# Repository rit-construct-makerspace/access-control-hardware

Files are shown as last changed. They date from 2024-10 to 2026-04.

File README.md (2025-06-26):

# Makerspace Access Control System

## Summary
There's a lot of equipment in a makerspace that can be dangerous to operate without proper training. To make sure only trained personnel are accessing equipment at the RIT SHED Makerspace, an access control system was developed. This system works off of student/faculty/staff NFC ID cards, and checks a central database (automatically updated by training programs) to ensure users are trained to use the machine they are trying to access. A number of different switching mechanisms are developed, to allow maximum flexibility in integration with a wide array of machines. 

### More information can be found on the [GitHub Wiki](https://github.com/rit-construct-makerspace/access-control-hardware/wiki).

### Firmware documented in a seperate repository; [access-control-firmware](https://github.com/rit-construct-makerspace/access-control-firmware).

## Current State
All components of the Access Control System have reached a stable and mature release, and are ready undergoing large-scale deployment testing across all 3 of our makerspaces.

## Instructions & Further Documentation
[See the wiki on GitHub!](https://github.com/rit-construct-makerspace/access-control-hardware/wiki) 

## Photos & Media
Coming Soon!

## License
This project is licensed under the CERN-OHL-S License. See LIECENSE.txt for more information.

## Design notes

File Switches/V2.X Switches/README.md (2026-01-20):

# V2.X Switch Backwards Compatibility

ACS version 2.X Switches are backwards compatible with ACS version 3.X Cores and similar. A DB9 to HD15 adapter for converting PS2 video to VGA video can be used to adapt the interface. The following pins of the DB9 are connected in these adapters;

* DB9 (Pin) - HD15 (Pin)
* 1 (Access) - 1 (Access)
* 2 (OneWire) - 2 (OneWire)
* 3 (Ground) - 3 (Ground)
* 4 (Power) - 13 (+5V)
* 5 (Ground) - Not Connected
* 6 (Type) - 6 (+5V)
* 7 (Interrupt) - 7 (Interrupt)
* 8 (Unused) - Not Connected
* 9 (Unused) - 10, 11 (Ground)

This is only suggested with short cable runs, as there is already a >500mV voltage drop from the switch's diode.

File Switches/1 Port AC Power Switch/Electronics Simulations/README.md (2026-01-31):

These files are meant to be opened in Falstad Circuit Simulator. See https://www.falstad.com/circuit/ for more information.

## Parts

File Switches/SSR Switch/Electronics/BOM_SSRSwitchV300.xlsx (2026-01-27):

No. | Quantity | Comment | Designator | Footprint | Value | Manufacturer Part | Manufacturer | Supplier Part | Supplier
1 | 2 | 100nF | C1,C2 | C0805 | 100nF | CL21B104KCFNNNE | SAMSUNG(三星) | C28233 | LCSC
2 | 1 | DS1038-15FBNSiA74-0CC | CN1 | DSUB-TH_DS1038-15FBNSIA74-0CC |  | DS1038-15FBNSiA74-0CC | CONNFLY | C75754 | LCSC
3 | 1 | XY308-2.54-5P | CN2 | CONN-TH_XY308-2.54-5P |  | XY308-2.54-5P | XINLAIYA(新莱亚) | C915914 | LCSC
4 | 1 | 921-111A1010D10200 | CN3 | USB-B_TH_USB-B-FEMALE-90 |  | 921-111A1010D10200 | 精拓金 | C46392 | LCSC
5 | 1 | MHK1560CRBTD | DS1 | LED-TH_MHK1560UGBTD |  | MHK1560CRBTD | MEIHUA(美华) | C7470835 | LCSC
6 | 1 | MHK1560UGBTD | DS2 | LED-TH_MHK1560UGBTD |  | MHK1560UGBTD | MEIHUA(美华) | C7470833 | LCSC
7 | 2 | MF-NSMF050-2 | F1,F2 | F1206 |  | MF-NSMF050-2 | BOURNS | C75464 | LCSC
8 | 1 | BLX-A-B | FH1 | FUSE-TH_BLX-A-B |  | BLX-A-B | XFCN(兴飞) | C41371862 | LCSC
9 | 2 | 390Ω | R3,R6 | R0805 | 390Ω | 0805W8F3900T5E | UNI-ROYAL(厚声) | C17655 | LCSC
10 | 1 | 10kΩ | R5 | R0805 | 10kΩ | 0805W8F1002T5E | UNI-ROYAL(厚声) | C17414 | LCSC
11 | 2 | 1kΩ | R7,R8 | R0805 | 1kΩ | 0805W8F1001T5E | UNI-ROYAL(厚声) | C17513 | LCSC
12 | 1 | TLP172AM(TPL,E | U1 | SOP-6_4P-L3.7-W4.6-P2.54-LS7.0-BL |  | TLP172AM(TPL,E | TOSHIBA(东芝) | C2152276 | LCSC
13 | 1 | DS18B20Z | U2 | SOP-8_L4.9-W3.9-P1.27-LS6.0-BL |  | DS18B20Z | UMW(友台半导体) | C695837 | LCSC
14 | 1 | MX5052S | U3 | SOP-8_L4.9-W3.9-P1.27-LS6.0-BL |  | MX5052S | Wuxi Maxinmicro(无锡明芯微) | C5875696 | LCSC

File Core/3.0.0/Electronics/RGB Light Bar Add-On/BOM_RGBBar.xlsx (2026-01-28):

No. | Quantity | Comment | Designator | Footprint | Value | Manufacturer Part | Manufacturer | Supplier Part | Supplier
1 | 9 | 100nF | C1,C2,C3,C4,C5,C6,C7,C8,C9 | C0805 | 100nF | CL21B104KCFNNNE | SAMSUNG(三星) | C28233 | LCSC
2 | 1 | B-3002N14P-0110 | CN3 | IDC-SMD_14P-P2.00_B-3002N14P-0110 |  | B-3002N14P-0110 | Ckmtw(灿科盟) | C383681 | LCSC
3 | 7 | WS2812B-V5/W | LED1,LED2,LED3,LED4,LED5,LED6,LED7 | LED-SMD_4P-L5.0-W5.0-TL-1 |  | WS2812B-V5/W | worldsemi | C2874885 | LCSC
4 | 2 | SMTSO3040CTJ | N1,N2 | SMD-1_BD5.5-D4.0_H4.0 |  | SMTSO3040CTJ | Sinhoo(雄和远景) | C2915635 | LCSC
5 | 1 | DS18B20Z | U1 | SOP-8_L4.9-W3.9-P1.27-LS6.0-BL |  | DS18B20Z | UMW(友台半导体) | C695837 | LCSC
6 | 1 | SN74AHCT125DR | U2 | SOIC-14_L8.7-W3.9-P1.27-LS6.0-BL |  | SN74AHCT125DR | TI(德州仪器) | C155176 | LCSC

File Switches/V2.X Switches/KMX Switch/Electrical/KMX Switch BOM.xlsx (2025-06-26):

No. | Quantity | Comment | Designator | Footprint | Value | Manufacturer Part | Manufacturer | Supplier Part | Supplier
1 | 2 | SS14 | D1,D2 | SMA_L4.2-W2.6-LS5.3-RD |  | SS14 | MDD | C2480 | LCSC
2 | 1 | MHK1560CRBTD | DS1 | LED-TH_MHK1560UGBTD |  | MHK1560CRBTD | MEIHUA(美华) | C7470835 | LCSC
3 | 1 | MHK1560UGBTD | DS2 | LED-TH_MHK1560UGBTD |  | MHK1560UGBTD | MEIHUA(美华) | C7470833 | LCSC
4 | 2 | Fuse Holder | F1,F2 | FUSE-TH_L24.5-W9.8-P22.5 |  | 保险丝透明座 | xcfuse(旭程) | C58066 | LCSC
5 | 2 | D-SUB-DR-9PCM-CB | J1,J3 | DB9-TH_ID09S33E4GV00LF |  | D-SUB-DR-9PCM-CB | XUNPU(讯普) | C19077337 | LCSC
6 | 1 | U-USBBR04P-F001 | J2 | USB-B-TH_U241-041N-1BR85-1 |  | U-USBBR04P-F001 | Ckmtw(灿科盟) | C386743 | LCSC
7 | 1 | TX2-5V | K1 | RELAY-TH_TX2-3V |  | TX2-5V | PANASONIC(松下) | C192257 | LCSC
8 | 3 | SMTSOM360BTR | MP1,MP2,MP3 | SMD_BD5.6-D4.1 |  | SMTSOM360BTR | YIYUAN(怡远) | C5221846 | LCSC
9 | 1 | D882 Y档160~320 | Q1 | SOT-89-3_L4.5-W2.5-P1.50-LS4.2-BR |  | D882 Y档160~320 | CJ(江苏长电/长晶) | C9634 | LCSC
10 | 3 | 1kΩ | R1,R3,R4 | R0805 | 1kΩ | 0805W8F1001T5E | UNI-ROYAL(厚声) | C17513 | LCSC
11 | 1 | 10kΩ | R2 | R0805 | 10kΩ | 0805W8F1002T5E | UNI-ROYAL(厚声) | C17414 | LCSC
12 | 1 | DS18B20Z | U1 | SOP-8_L4.9-W3.9-P1.27-LS6.0-BL |  | DS18B20Z | UMW(友台半导体) | C695837 | LCSC

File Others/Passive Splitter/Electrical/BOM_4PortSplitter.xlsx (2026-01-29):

No. | Quantity | Comment | Designator | Footprint | Value | Manufacturer Part | Manufacturer | Supplier Part | Supplier
1 | 8 | MINISMDC200F/16-2 | F1,F2,F3,F4,F5,F6,F7,F8 | R1812 |  | MINISMDC200F/16-2 | Littelfuse(美国力特) | C315963 | LCSC
2 | 4 | DS1038-15FBNSiA74-0CC | J1,J2,J3,J4 | DSUB-TH_DS1038-15FBNSIA74-0CC |  | DS1038-15FBNSiA74-0CC | CONNFLY | C75754 | LCSC
3 | 4 | DS-04-R-T | SW1,SW2,SW3,SW4 | SW-TH_8P-L11.6-W9.9-P2.54_WT11-DS-04RR |  | DS-04-R-T | 康深 | C5123702 | LCSC
4 | 1 | DS18B20Z | U1 | SOP-8_L4.9-W3.9-P1.27-LS6.0-BL |  | DS18B20Z | UMW(友台半导体) | C695837 | LCSC

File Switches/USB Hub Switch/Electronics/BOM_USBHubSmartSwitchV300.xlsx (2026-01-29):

No. | Quantity | Comment | Designator | Footprint | Value | Manufacturer Part | Manufacturer | Supplier Part | Supplier
1 | 11 | 10uF | C1,C2,C4,C6,C7,C8,C13,C18,C23,C28,C29 | C0603 | 10uF | CL10A106MA8NRNC | SAMSUNG(三星) | C96446 | LCSC
2 | 3 | 1uF | C5,C30,C32 | C0603 | 1uF | CL10A105KB8NNNC | SAMSUNG(三星) | C15849 | LCSC
3 | 13 | 47uF | C9,C10,C11,C14,C15,C16,C19,C20,C21,C24,C25,C26,C36 | C1206 | 47uF | CL31A476MPHNNNE | SAMSUNG(三星) | C96123 | LCSC
4 | 7 | 100nF | C12,C17,C22,C27,C31,C33,C35 | C0603 | 100nF | CC0603KRX7R9BB104 | YAGEO(国巨) | C14663 | LCSC
5 | 1 | DS1038-15FBNSiA74-0CC | CN1 | DSUB-TH_DS1038-15FBNSIA74-0CC |  | DS1038-15FBNSiA74-0CC | CONNFLY | C75754 | LCSC
6 | 1 | HC-TYPE-C-16P-067A | CN2 | USB-SMD_HC-TYPE-C-16P-FLS7.2-5A-11 |  | HC-TYPE-C-16P-067A | HC(虹成电子) | C48887186 | LCSC
7 | 4 | 902-131A1011D10100 | CN3,CN4,CN5,CN6 | USB-A-TH__USB-AF-90 |  | 902-131A1011D10100 | 精拓金 | C2345 | LCSC
8 | 8 | SRV05-4 | D1,D2,D3,D4,D5,D6,D7,D8 | SOT-23-6_L2.9-W1.6-P0.95-LS2.8-BL |  | SRV05-4 | TECH PUBLIC(台舟) | C558418 | LCSC
9 | 4 | TZ-LAMP05RB4HD-C | LED1,LED2,LED3,LED4 | LED-TH_3P-BD5.8-P2.54-R-BI |  | TZ-LAMP05RB4HD-C | TUOZHAN(拓展光电) | C779425 | LCSC
10 | 17 | 10kΩ | R1,R3,R4,R5,R6,R18,R19,R20,R21,R22,R23,R24,R25,R33,R34,R35,R36 | R0603 | 10kΩ | 0603WAF1002T5E | UNI-ROYAL(厚声) | C25804 | LCSC
11 | 10 | 120kΩ | R2,R7,R8,R9,R10,R11,R14,R15,R16,R17 | R0603 | 120kΩ | 0603WAF1203T5E | UNI-ROYAL(厚声) | C25808 | LCSC
12 | 2 | 5.1kΩ | R12,R13 | R0603 | 5.1kΩ | 0603WAF5101T5E | UNI-ROYAL(厚声) | C23186 | LCSC
13 | 4 | 1kΩ | R26,R27,R28,R29 | R0805 | 1kΩ | 0805W8F1001T5E | UNI-ROYAL(厚声) | C17513 | LCSC
14 | 3 | 0Ω | R37,R38,R39 | R0805 | 0Ω | 0805W8F0000T5E | UNI-ROYAL(厚声) | C17477 | LCSC
15 | 1 | SL2.1A | U1 | SOP-16_L10.0-W3.9-P1.27-LS6.0-BL |  | SL2.1A | CoreChips(和芯润德) | C192893 | LCSC
16 | 1 | DS18B20Z | U2 | SOP-8_L4.9-W3.9-P1.27-LS6.0-BL |  | DS18B20Z | UMW(友台半导体) | C695837 | LCSC
17 | 1 | MX66100T | U3 | SOT-23-6_L2.9-W1.6-P0.95-LS2.9-BL |  | MX66100T | Wuxi Maxinmicro(无锡明芯微) | C53121238 | LCSC
18 | 5 | CH217K | U4,U5,U7,U9,U11 | SOT-23-6_L2.9-W1.6-P0.95-LS2.8-BL |  | CH217K | WCH(南京沁恒) | C7462749 | LCSC
19 | 4 | DIO32220MP10 | U6,U8,U10,U12 | MSOP-10_L3.0-W3.0-P0.50-LS5.0-BL |  | DIO32220MP10 | DIOO(帝奥微) | C444624 | LCSC
20 | 1 | STM8S003F3P6TR | U13 | TSSOP-20_L6.5-W4.4-P0.65-LS6.4-BL |  | STM8S003F3P6TR | ST(意法半导体) | C52717 | LCSC
21 | 1 | 74HC595D,118 | U14 | SOIC-16_L9.9-W3.9-P1.27-LS6.0-BL |  | 74HC595D,118 | Nexperia(安世) | C5947 | LCSC
22 | 1 | 12MHz | X1 | OSC-SMD_4P-L3.2-W2.5-BL | 12MHz | X322512MSB4SI | YXC(扬兴晶振) | C9002 | LCSC

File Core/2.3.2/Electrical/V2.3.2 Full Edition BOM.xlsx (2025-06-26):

No. | Quantity | Comment | Designator | Footprint | Value | Manufacturer Part | Manufacturer | Supplier Part | Supplier
1 | 32 | 100nF | C1,C4,C5,C6,C7,C8,C9,C10,C11,C12,C13,C14,C17,C18,C19,C20,C21,C27,C28,C29,C32,C34,C35,C42,C46,C48,C50,C51,C52,C53,C54,C55 | C0603 | 100nF | CC0603KRX7R9BB104 | YAGEO(国巨) | C14663 | LCSC
2 | 19 | 10uF | C2,C3,C15,C16,C24,C25,C26,C30,C36,C37,C38,C39,C40,C41,C43,C44,C45,C47,C49 | C0603 | 10uF | CL10A106MA8NRNC | SAMSUNG(三星) | C96446 | LCSC
3 | 3 | 1uF | C22,C31,C33 | C0603 | 1uF | CL10A105KB8NNNC | SAMSUNG(三星) | C15849 | LCSC
4 | 2 | 4.7uF | C23,C57 | C0603 | 4.7uF | CL10A475KO8NNNC | SAMSUNG(三星) | C19666 | LCSC
5 | 2 | 33pF | C56,C59 | C0603 | 33pF | CL10C330JB8NNNC | SAMSUNG(三星) | C1663 | LCSC
6 | 3 | 10nF | C58,C62,C63 | C0603 | 10nF | 0603B103K500NT | FH(风华) | C57112 | LCSC
7 | 2 | 6.8nF | C60,C61 | C0603 | 6.8nF | C1608X7R2A682KT000N | TDK | C694293 | LCSC
8 | 1 | SM4007PL | D1 | SOD-123F_L2.8-W1.8-LS3.7-RD |  | SM4007PL | MDD | C64898 | LCSC
9 | 1 | 1N4148W | D2 | SOD-123F_L2.7-W1.6-LS3.8-RD |  | 1N4148W | ST(先科) | C81598 | LCSC
10 | 1 | SRV05-4-P-T7 | D3 | SOT-23-6_L2.9-W1.6-P0.95-LS2.8-BR |  | SRV05-4-P-T7 | PROTEK | C85364 | LCSC
11 | 1 | SS14 | D4 | SMA_L4.2-W2.6-LS5.3-RD |  | SS14 | MDD | C2480 | LCSC
12 | 2 | KT-0603R | DS1,DS2 | LED0603-RD |  | KT-0603R | KENTO | C2286 | LCSC
13 | 2 | MH2029-300Y | FB1,FB2 | L0805 |  | MH2029-300Y | BOURNS | C840593 | LCSC
14 | 3 | DB127S-3.5-4P-GN | J1,J2,J3 | CONN-TH_4P-P3.50_DIBO_DB127S-3.5-4P-GN |  | DB127S-3.5-4P-GN | DORABO(地博电气) | C2997511 | LCSC
15 | 1 | PM254-1-08-W-8.5 | J4 | HDR-TH_8P-P2.54-H-F-W10.0-N |  | PM254-1-08-W-8.5 | HCTL(华灿天禄) | C2897390 | LCSC
16 | 1 | U-USBBR04P-F001 | J5 | USB-B-TH_U241-041N-1BR85-1 |  | U-USBBR04P-F001 | Ckmtw(灿科盟) | C386743 | LCSC
17 | 1 | D-SUB-DR-9PCM-CB | J6 | DB9-TH_ID09S33E4GV00LF |  | D-SUB-DR-9PCM-CB | XUNPU(讯普) | C19077337 | LCSC
18 | 1 | HC913129AE-907-A | J7 | RJ45-TH_HC911102A-904-A |  | HC913129AE-907-A | HCTL(华灿天禄) | C5341218 | LCSC
19 | 1 | 2.7kHz | LS1 | BUZ-SMD_4P-L8.5-W8.5-P8.50-TL | 2.7kHz | MLT-8540 | 华能 | C95300 | LCSC
20 | 4 | SMTSO2070CTJ | MP1,MP2,MP3,MP4 | SMD_BD5.6-L5.6-W5.6-D3.6 |  | SMTSO2070CTJ | Sinhoo(雄和远景) | C2916355 | LCSC
21 | 4 | S8050 J3Y | Q1,Q2,Q3,Q4 | SOT-23-3_L3.0-W1.7-P0.95-LS2.9-BR |  | S8050 J3Y | CJ(江苏长电/长晶) | C2146 | LCSC
22 | 5 | 100kΩ | R1,R3,R4,R5,R6 | R0603 | 100kΩ | 0603WAF1003T5E | UNI-ROYAL(厚声) | C25803 | LCSC
23 | 3 | 1kΩ | R2,R45,R46 | R0603 | 1kΩ | 0603WAF1001T5E | UNI-ROYAL(厚声) | C21190 | LCSC
24 | 3 | 4.7kΩ | R7,R17,R18 | R0603 | 4.7kΩ | 0603WAF4701T5E | UNI-ROYAL(厚声) | C23162 | LCSC
25 | 1 | 470Ω | R8 | R0603 | 470Ω | 0603WAF4700T5E | UNI-ROYAL(厚声) | C23179 | LCSC
26 | 28 | 10kΩ | R9,R10,R11,R12,R13,R14,R15,R16,R19,R20,R21,R22,R23,R25,R26,R27,R28,R29,R30,R31,R32,R33,R34,R35,R36,R38,R39,R41 | R0603 | 10kΩ | 0603WAF1002T5E | UNI-ROYAL(厚声) | C25804 | LCSC
27 | 1 | 5.1kΩ | R24 | R0603 | 5.1kΩ | 0603WAF5101T5E | UNI-ROYAL(厚声) | C23186 | LCSC
28 | 1 | 12.4kΩ | R37 | R0603 | 12.4kΩ | RTT031242FTP | RALEC(旺诠) | C103261 | LCSC
29 | 1 | 1MΩ | R40 | R0603 | 1MΩ | 0603WAF1004T5E | UNI-ROYAL(厚声) | C22935 | LCSC
30 | 4 | 49.9Ω | R42,R43,R47,R48 | R0603 | 49.9Ω | 0603WAF1002T5E | UNI-ROYAL(厚声) | C859049 | LCSC
31 | 1 | 10Ω | R44 | R0603 | 10Ω | 0603WAF100JT5E | UNI-ROYAL(厚声) | C22859 | LCSC
32 | 2 | K9-1267F | SW1,SW2 | SW-TH_K9-1267F |  | K9-1267F | 韩国韩荣 | C107263 | LCSC
33 | 1 | KH-10027B-SMT2.54-6P | SW3 | SW-SMD_KINGHELM_KH-10027B-SMT2.54-6P |  | KH-10027B-SMT2.54-6P | kinghelm(金航标) | C2842912 | LCSC
34 | 8 | SN74LVC1G17DBVR | U1,U2,U3,U4,U5,U6,U7,U18 | SOT-23-5_L3.0-W1.7-P0.95-LS2.8-BR |  | SN74LVC1G17DBVR | TI(德州仪器) | C7836 | LCSC
35 | 1 | ATTINY3216-SNR | U8 | SOIC-20_L12.8-W7.5-P1.27-LS10.3-BL |  | ATTINY3216-SNR | MICROCHIP(美国微芯) | C609661 | LCSC
36 | 3 | CH340C | U9,U10,U15 | SOP-16_L10.0-W3.9-P1.27-LS6.0-BL |  | CH340C | WCH(南京沁恒) | C84681 | LCSC
37 | 1 | BL8565CC3BTR33 | U11 | SOT-89-3_L4.5-W2.5-P1.50-LS4.2-BR |  | BL8565CC3BTR33 | BL(上海贝岭) | C51826 | LCSC
38 | 1 | ESP32-S2-SOLO-2-N4 | U12 | WIRELM-SMD_ESP32-S3-WROOM-1 | 2.4GHz | ESP32-S2-SOLO-2-N4 | ESPRESSIF(乐鑫) | C3040594 | LCSC
39 | 4 | MT9700 | U13,U17,U19,U22 | SOT-23-5_L3.0-W1.7-P0.95-LS2.8-BR |  | MT9700 | 西安航天民芯 | C89855 | LCSC
40 | 1 | DS18B20Z | U14 | SOP-8_L4.9-W3.9-P1.27-LS6.0-BL |  | DS18B20Z | UMW(友台半导体) | C695837 | LCSC
41 | 1 | SL2.1A | U16 | SOP-16_L10.0-W3.9-P1.27-LS6.0-BL |  | SL2.1A | CoreChips(和芯润德) | C192893 | LCSC
42 | 1 | MAX811T | U20 | SOT-143-4_L2.9-W1.3-P1.90-LS2.4-BL-1 |  | MAX811T | TECH PUBLIC(台舟) | C19631730 | LCSC
43 | 1 | SN74AHC1G125DBVR | U21 | SOT-23-5_L3.0-W1.7-P0.95-LS2.8-BR |  | SN74AHC1G125DBVR | TI(德州仪器) | C7468 | LCSC
44 | 1 | W5500 | U23 | LQFP-48_L7.0-W7.0-P0.50-LS9.0-BL |  | W5500 | WIZNET | C32843 | LCSC
45 | 1 | 12MHz | X1 | OSC-SMD_4P-L3.2-W2.5-BL | 12MHz | X322512MSB4SI | YXC(扬兴晶振) | C9002 | LCSC
46 | 1 | 25MHz | X2 | CRYSTAL-SMD_4P-L2.5-W2.0-BL | 25MHz | 7E25000E20UCG | SJK(晶科鑫) | C252264 | LCSC

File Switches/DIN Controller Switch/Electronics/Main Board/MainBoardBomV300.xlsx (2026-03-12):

No. | Quantity | Comment | Designator | Footprint | Value | Manufacturer Part | Manufacturer | Supplier Part | Supplier
1 | 2 | 1nF | C1,C5 | CAP-TH_L6.3-W4.4-P10.00-D0.6-S3.8 | 1nF | CY1102ME14EF45W2A2 | Dersonic(德尔创) | C2974845 | LCSC
2 | 1 | 100nF | C2 | CAP-TH_L13.0-W6.0-P10.00-D1.0 | 100nF | MP2104K27C3X6LC | SRD(圣融达) | C105759 | LCSC
3 | 3 | 1uF | C3,C8,C9 | C0805 | 1uF | CL21B105KBFNNNE | SAMSUNG(三星) | C28323 | LCSC
4 | 1 | 470uF | C4 | CAP-TH_BD10.0-P5.00-D1.0-FD | 470uF | ERS1VM471G16OT | AISHI(艾华集团) | C106703 | LCSC
5 | 4 | 100nF | C6,C7,C10,C11 | C0805 | 100nF | CL21B104KCFNNNE | SAMSUNG(三星) | C28233 | LCSC
6 | 4 | DB128V-5.08-9P-GN-S | CN1,CN2,CN3,CN5 | CONN-TH_9P-P5.08_DIBO_DB128V-5.08-9P-GN-S |  | DB128V-5.08-9P-GN-S | DORABO(地博电气) | C2938972 | LCSC
7 | 1 | X1270WV-2x05B-9TV01 | CN4 | IDC-TH_10P-P1.27-X1270WV-2X05A-6TV01 |  | X1270WV-2x05B-9TV01 | XKB Connection(中国星坤) | C2962225 | LCSC
8 | 1 | SMBJ15A | D1 | SMB_L4.3-W3.6-LS5.3-RD |  | SMBJ15A | R+O(宏嘉诚) | C19077569 | LCSC
9 | 3 | SRV05-4 | D2,D3,D7 | SOT-23-6_L2.9-W1.6-P0.95-LS2.8-BL-1 |  | SRV05-4 | R+O(宏嘉诚) | C7420376 | LCSC
10 | 3 | SMF12A | D4,D5,D6 | SOD-123FL_L2.8-W1.8-LS3.8-R-RD |  | SMF12A | R+O(宏嘉诚) | C19077506 | LCSC
11 | 1 | 05200101Z | FH1 | BAT-TH_05200101Z |  | 05200101Z | Littelfuse(美国力特) | C142924 | LCSC
12 | 5 | G2RL-1-DC12 | K1,K2,K3,K4,K5 | RELAY-TH_G2RL-1-DCXX |  | G2RL-1-DC12 | OMRON(欧姆龙) | C469130 | LCSC
13 | 1 | EE8.3-15mH | L1 | XFMR-TH_4P-L9.5-W9.5_EE8.3-10MH |  | EE8.3-15mH | NYBOXING(尼博星) | C18870246 | LCSC
14 | 1 | 470uH | L2 | IND-TH_BD8.7-P5.0-D0.7_RLB0914 | 470uH | RLB0914-471KL | BOURNS | C7051049 | LCSC
15 | 1 | 210pF@1kHz | R1 | RES-TH_L12.5-W5.1-P7.50-D1.2-S2.20 | 210pF@1kHz | VDR-10D471K | VDR(嵩隆) | C316609 | LCSC
16 | 2 | 390Ω | R2,R4 | R0805 | 390Ω | 0805W8F3900T5E | UNI-ROYAL(厚声) | C17655 | LCSC
17 | 8 | 20kΩ | R3,R6,R7,R12,R13,R14,R15,R16 | R0805 | 20kΩ | 0805W8F2002T5E | UNI-ROYAL(厚声) | C4328 | LCSC
18 | 1 | 100kΩ | R5 | R0805 | 100kΩ | 0805W8F1003T5E | UNI-ROYAL(厚声) | C149504 | LCSC
19 | 3 | 10kΩ | R8,R9,R10 | R0805 | 10kΩ | 0805W8F1002T5E | UNI-ROYAL(厚声) | C17414 | LCSC
20 | 1 | 5.1kΩ | R11 | R0805 | 5.1kΩ | 0805W8F5101T5E | UNI-ROYAL(厚声) | C27834 | LCSC
21 | 2 | MX5052S | U1,U5 | SOP-8_L4.9-W3.9-P1.27-LS6.0-BL |  | MX5052S | Wuxi Maxinmicro(无锡明芯微) | C5875696 | LCSC
22 | 1 | TAS20-12-W2 | U2 | PWRM-TH_4P-L39.0-W25.0_TAS12-15-W2 |  | TAS20-12-W2 | TDPOWER(腾达电源) | C39846906 | LCSC
23 | 1 | DS18B20Z(UMW) | U3 | SOP-8_L4.9-W3.9-P1.27-LS6.0-BL |  | DS18B20Z(UMW) | UMW(友台半导体) | C695837 | LCSC
24 | 1 | MX25947ES | U4 | ESOP-8_L4.9-W3.9-P1.27-LS6.0-BL-EP-1 |  | MX25947ES | Wuxi Maxinmicro(无锡明芯微) | C5875698 | LCSC
25 | 1 | ULN2003ADR | U6 | SOIC-16_L9.9-W3.9-P1.27-LS6.0-BL |  | ULN2003ADR | TI(德州仪器) | C7512 | LCSC
26 | 1 | 74HC08D,653 | U7 | SOIC-14_L8.7-W3.9-P1.27-LS6.0-BL |  | 74HC08D,653 | Nexperia(安世) | C5593 | LCSC

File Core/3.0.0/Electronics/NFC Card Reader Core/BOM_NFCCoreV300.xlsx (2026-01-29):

No. | Quantity | Comment | Designator | Footprint | Value | Manufacturer Part | Manufacturer | Supplier Part | Supplier
1 | 1 | 2.7kHz | BZR1 | BUZ-SMD_4P-L8.5-W8.5-P8.50-TL | 2.7kHz | MLT-8540 | 华能 | C95300 | LCSC
2 | 2 | 12pF | C1,C7 | C0603 | 12pF | CL10C120JB8NNNC | SAMSUNG(三星) | C38523 | LCSC
3 | 2 | 470nF | C2,C4 | C0603 | 470nF | CL10B474KA8NNNC | SAMSUNG(三星) | C1623 | LCSC
4 | 39 | 100nF | C3,C6,C8,C13,C14,C15,C16,C23,C24,C26,C27,C31,C32,C33,C34,C35,C36,C39,C40,C43,C44,C53,C59,C64,C71,C73,C74,C76,C77,C78,C79,C80,C81,C93,C94,C95,C96,C97,C98 | C0603 | 100nF | CC0603KRX7R9BB104 | YAGEO(国巨) | C14663 | LCSC
5 | 4 | 1uF | C5,C29,C60,C90 | C0603 | 1uF | CL10A105KB8NNNC | SAMSUNG(三星) | C15849 | LCSC
6 | 2 | 1nF | C9,C20 | C0603 | 1nF | CL10B102KB8NNNC | SAMSUNG(三星) | C1588 | LCSC
7 | 2 | 68pF | C10,C19 | C0603 | 68pF | CL10C680JB8NNNC | SAMSUNG(三星) | C28262 | LCSC
8 | 4 | 120pF | C11,C12,C17,C18 | C0603 | 120pF | CL10C121JB8NNNC | SAMSUNG(三星) | C18438 | LCSC
9 | 5 | 47uF | C21,C22,C41,C42,C55 | C1206 | 47uF | CL31A476MPHNNNE | SAMSUNG(三星) | C96123 | LCSC
10 | 4 | 10nF | C25,C85,C87,C89 | C0603 | 10nF | 0603B103K500NT | FH(风华) | C57112 | LCSC
11 | 26 | 10uF | C28,C30,C37,C38,C45,C46,C47,C48,C49,C51,C52,C54,C56,C57,C61,C62,C63,C65,C66,C67,C68,C69,C72,C75,C91,C92 | C0603 | 10uF | CL10A106MA8NRNC | SAMSUNG(三星) | C96446 | LCSC
12 | 1 | 30pF | C50 | C0603 | 30pF | 0603CG300J500NT | FH(风华) | C1658 | LCSC
13 | 2 | 33nF | C58,C70 | C0603 | 33nF | CL10B333KB8NNNC | SAMSUNG(三星) | C21117 | LCSC
14 | 2 | 18pF | C82,C88 | C0603 | 18pF | CL10C180JB8NNNC | SAMSUNG(三星) | C1647 | LCSC
15 | 2 | 6.8nF | C83,C84 | C0603 | 6.8nF | 0603B682K500NT | FH(风华) | C1631 | LCSC
16 | 1 | 4.7uF | C86 | C0603 | 4.7uF | CL10A475KO8NNNC | SAMSUNG(三星) | C19666 | LCSC
17 | 1 | B-3002N14P-0110 | CN1 | IDC-SMD_14P-P2.00_B-3002N14P-0110 |  | B-3002N14P-0110 | Ckmtw(灿科盟) | C383681 | LCSC
18 | 1 | HC-GAP-ACF012-1T | CN2 | USB-C-SMD_HC-GAP-ACF012-1T-1 |  | HC-GAP-ACF012-1T | HCTL(华灿天禄) | C2894906 | LCSC
19 | 1 | DS1038-15FBNSiA74-0CC | CN3 | DSUB-TH_DS1038-15FBNSIA74-0CC |  | DS1038-15FBNSiA74-0CC | CONNFLY | C75754 | LCSC
20 | 1 | HC913129AE-907-A | CN4 | RJ45-TH_HC911102A-904-A |  | HC913129AE-907-A | HCTL(华灿天禄) | C5341218 | LCSC
21 | 3 | SRV05-4 | D1,D5,D9 | SOT-23-6_L2.9-W1.6-P0.95-LS2.8-BL |  | SRV05-4 | TECH PUBLIC(台舟) | C558418 | LCSC
22 | 1 | SMFJ12A | D2 | SOD-123F_L2.8-W1.8-LS3.7-RD |  | SMFJ12A | RUILON(瑞隆源) | C82280 | LCSC
23 | 1 | PTVS3V3S1UR,115 | D3 | SOD-123_L2.8-W1.8-LS3.7-RD |  | PTVS3V3S1UR,115 | Nexperia(安世) | C183521 | LCSC
24 | 3 | B5819W SL | D6,D7,D8 | SOD-123_L2.7-W1.6-LS3.7-RD-1 |  | B5819W SL | CJ(江苏长电/长晶) | C8598 | LCSC
25 | 4 | SMD1206B050TF | F1,F2,F3,F7 | F1206 |  | SMD1206B050TF | Brightking(君耀电子) | C269115 | LCSC
26 | 3 | JK-nSMD100-16 | F4,F5,F6 | F1206 |  | JK-nSMD100-16 | JK(金科) | C369161 | LCSC
27 | 2 | MH2029-300Y | FB1,FB2 | L0805 |  | MH2029-300Y | BOURNS | C840593 | LCSC
28 | 1 | HDR-M_2.54_1x4P | H1 | HDR-TH_4P-P2.54-V-M
29 | 2 | 470nH | L1,L2 | L0603 | 470nH | MLP1608VR47DT0S1 | TDK | C105533 | LCSC
30 | 2 | 4.7uH | L3,L4 | IND-SMD_L7.1-W6.6 | 4.7uH | PSPMAA0605H-4R7M-ANP | PROD(谱罗德) | C2983090 | LCSC
31 | 1 | KT-0603R | LED1 | LED0603-RD |  | KT-0603R | KENTO | C2286 | LCSC
32 | 2 | WS2812D-F8 | LED2,LED3 | LED-TH_WS2812D-F8 |  | WS2812D-F8 | worldsemi | C139126 | LCSC
33 | 5 | SMTSO3060CTJ | M1,M2,M3,M4,M5 | SMD_SMTSO3060CTJ |  | SMTSO3060CTJ | Sinhoo(雄和远景) | C2915637 | LCSC
34 | 1 | S8050 J3Y | Q1 | SOT-23-3_L3.0-W1.7-P0.95-LS2.9-BR |  | S8050 J3Y | CJ(江苏长电/长晶) | C2146 | LCSC
35 | 15 | 10kΩ | R1,R2,R19,R20,R21,R22,R25,R26,R27,R28,R30,R35,R37,R40,R49 | R0603 | 10kΩ | 0603WAF1002T5E | UNI-ROYAL(厚声) | C25804 | LCSC
36 | 10 | 1kΩ | R3,R10,R14,R31,R32,R34,R42,R44,R47,R55 | R0603 | 1kΩ | 0603WAF1001T5E | UNI-ROYAL(厚声) | C21190 | LCSC
37 | 3 | 22kΩ | R4,R9,R29 | R0603 | 22kΩ | 0603WAF2202T5E | UNI-ROYAL(厚声) | C31850 | LCSC
38 | 3 | 100kΩ | R5,R6,R11 | R0603 | 100kΩ | 0603WAF1003T5E | UNI-ROYAL(厚声) | C25803 | LCSC
39 | 2 | 5.1Ω | R7,R8 | R0603 | 5.1Ω | 0603WAF510KT5E | UNI-ROYAL(厚声) | C25197 | LCSC
40 | 2 | 5.1kΩ | R12,R13 | R0603 | 5.1kΩ | 0603WAF5101T5E | UNI-ROYAL(厚声) | C23186 | LCSC
41 | 9 | 4.7kΩ | R15,R16,R17,R18,R23,R24,R50,R51,R56 | R0603 | 4.7kΩ | 0603WAF4701T5E | UNI-ROYAL(厚声) | C23162 | LCSC
42 | 1 | 51kΩ | R33 | R0603 | 51kΩ | 0603WAF5102T5E | UNI-ROYAL(厚声) | C23196 | LCSC
43 | 1 | 12.4kΩ | R36 | R0603 | 12.4kΩ | RTT031242FTP | RALEC(旺诠) | C103261 | LCSC
44 | 4 | 49.9Ω | R38,R39,R45,R46 | R0603 | 49.9Ω | 0603WAF1002T5E | UNI-ROYAL(厚声) | C859049 | LCSC
45 | 1 | 10Ω | R41 | R0603 | 10Ω | 0603WAF100JT5E | UNI-ROYAL(厚声) | C22859 | LCSC
46 | 1 | 1MΩ | R43 | R0603 | 1MΩ | 0603WAF1004T5E | UNI-ROYAL(厚声) | C22935 | LCSC
47 | 2 | 0Ω | R52,R53 | R0805 | 0Ω | 0805W8F0000T5E | UNI-ROYAL(厚声) | C17477 | LCSC
48 | 1 | 75Ω | R54 | R0603 | 75Ω | 0603WAF750JT5E | UNI-ROYAL(厚声) | C4275 | LCSC
49 | 2 | K9-1267F | SW1,SW2 | SW-TH_K9-1267F |  | K9-1267F | 韩国韩荣 | C107263 | LCSC
50 | 1 | TS-1045-A13B3-D2 | SW3 | SW-SMD_L7.5-W8.0-P4.50_TS-1045-A13B3-D2 |  | TS-1045-A13B3-D2 | Yuandi(元迪) | C557898 | LCSC
51 | 1 | MFRC63003HNE | U1 | HVQFN-32_L5.0-W5.0-P0.50-TL-EP3.1 |  | MFRC63003HNE | NXP(恩智浦) | C1526298 | LCSC
52 | 3 | SN74LVC1G17DBVR | U2,U3,U4 | SOT-23-5_L3.0-W1.7-P0.95-LS2.8-BR |  | SN74LVC1G17DBVR | TI(德州仪器) | C7836 | LCSC
53 | 1 | TMP112AIDRLR | U5 | SOT-563_L1.6-W1.2-P0.50-LS1.6-BR |  | TMP112AIDRLR | TI(德州仪器) | C28927 | LCSC
54 | 1 | LIS2DH12TR | U6 | LGA-12_L2.0-W2.0-P0.50-BL |  | LIS2DH12TR | ST(意法半导体) | C110926 | LCSC
55 | 2 | MX66100T | U7,U14 | SOT-23-6_L2.9-W1.6-P0.95-LS2.9-BL |  | MX66100T | Wuxi Maxinmicro(无锡明芯微) | C53121238 | LCSC
56 | 7 | SN74LVC1T45DBVR | U8,U9,U10,U11,U12,U19,U20 | SOT-23-6_L2.9-W1.6-P0.95-LS2.8-BR |  | SN74LVC1T45DBVR | TI(德州仪器) | C7843 | LCSC
57 | 2 | TPS62933DRLR | U13,U15 | SOT-583-8_L2.1-W1.2-P0.50-LS1.6-BR |  | TPS62933DRLR | TI(德州仪器) | C3200405 | LCSC
58 | 1 | SN74AHC1G125DBVR | U16 | SOT-23-5_L3.0-W1.7-P0.95-LS2.8-BR |  | SN74AHC1G125DBVR | TI(德州仪器) | C7468 | LCSC
59 | 1 | W5500 | U17 | LQFP-48_L7.0-W7.0-P0.50-LS9.0-BL |  | W5500 | WIZNET | C32843 | LCSC
60 | 1 | 2.4GHz | U18 | BULETM-SMD_ESP32-S3-MINI-1-N8 | 2.4GHz | ESP32-S3-MINI-1-N8 | ESPRESSIF(乐鑫) | C2913206 | LCSC
61 | 1 | 27.12MHz | X1 | CRYSTAL-SMD_4P-L3.2-W2.5-BL-1 | 27.12MHz | X32252712MMB4SI | YXC(扬兴晶振) | C29975 | LCSC
62 | 1 | 25MHz | X2 | CRYSTAL-SMD_4P-L3.2-W2.5-BL | 25MHz | X322525MOB4SI | YXC(扬兴晶振) | C9006 | LCSC

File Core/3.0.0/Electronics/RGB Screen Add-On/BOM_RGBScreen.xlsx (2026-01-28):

No. | Quantity | Comment | Designator | Footprint | Value | Manufacturer Part | Manufacturer | Supplier Part | Supplier
1 | 3 | 100nF | C1,C4,C10 | C0603 | 100nF | CC0603KRX7R9BB104 | YAGEO(国巨) | C14663 | LCSC
2 | 8 | 1uF | C2,C3,C5,C6,C7,C8,C9,C15 | C0603 | 1uF | CL10A105KB8NNNC | SAMSUNG(三星) | C15849 | LCSC
3 | 5 | 2.2uF | C11,C12,C13,C14,C16 | C0603 | 2.2uF | CL10A225KO8NNNC | SAMSUNG(三星) | C23630 | LCSC
4 | 1 | B-3002N14P-0110 | CN1 | IDC-SMD_14P-P2.00_B-3002N14P-0110 |  | B-3002N14P-0110 | Ckmtw(灿科盟) | C383681 | LCSC
5 | 4 | SMTSO3040CTJ | N1,N2,N3,N4 | SMD-1_BD5.5-D4.0_H4.0 |  | SMTSO3040CTJ | Sinhoo(雄和远景) | C2915635 | LCSC
6 | 6 | 0Ω | R1,R2,R7,R8,R9,R10 | R0805 | 0Ω | 0805W8F0000T5E | UNI-ROYAL(厚声) | C17477 | LCSC
7 | 3 | 20Ω | R4,R5,R6 | R1206 | 20Ω | 1206W4F200JT5E | UNI-ROYAL(厚声) | C17955 | LCSC
8 | 5 | 10kΩ | R11,R12,R13,R14,R15 | R0603 | 10kΩ | 0603WAF1002T5E | UNI-ROYAL(厚声) | C25804 | LCSC
9 | 1 | DS18B20Z | U1 | SOP-8_L4.9-W3.9-P1.27-LS6.0-BL |  | DS18B20Z | UMW(友台半导体) | C695837 | LCSC
10 | 1 | AP7380-30Y-13 | U2 | SOT-89-3_L4.5-W2.5-P1.50-LS4.2-BR |  | AP7380-30Y-13 | DIODES(美台) | C555162 | LCSC
11 | 1 | TLC59731DR | U3 | SOIC-8_L4.9-W3.8-P1.27-LS6.0-BL |  | TLC59731DR | TI(德州仪器) | C702091 | LCSC
12 | 1 | CD74HC4050M96 | U4 | SOIC-16_L9.9-W3.9-P1.27-LS6.0-BL |  | CD74HC4050M96 | TI(德州仪器) | C131932 | LCSC
13 | 1 | NHD-C12864DA-FSRGB-FBW-3V3 | U5 | LCD-TH_L58.2-W41.7-P1.27_NHD-C12864DA-FSRGB-FBW-3V3 |  | NHD-C12864DA-FSRGB-FBW-3V3 |  | C9900242902 | LCSC

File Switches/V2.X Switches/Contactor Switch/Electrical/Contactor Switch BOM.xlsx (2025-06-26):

No. | Quantity | Comment | Designator | Footprint | Value | Manufacturer Part | Manufacturer | Supplier Part | Supplier
1 | 2 | 10uF | C1,C2 | C0603 | 10uF | CL10A106MA8NRNC | SAMSUNG(三星) | C96446 | LCSC
2 | 2 | Y1 102M | C3,C7 | CAP-TH_L8.5-W5.0-P10.00-D0.6 | 1nF | VY1102M31Y5UC63V0 | VISHAY(威世) | C1620957 | LCSC
3 | 1 | X2 104K | C4 | CAP-TH_L10.0-W5.0-P7.50-D0.6 | 100nF | PX104K2C0702 | KYET(科雅) | C2693793 | LCSC
4 | 1 | 1uF | C5 | C1206 | 1uF | CL31B105KBHNNNE | SAMSUNG(三星) | C1848 | LCSC
5 | 1 | 470uF | C6 | CAP-TH_BD8.0-P3.50-D0.6-FD | 470uF | NXA 16V470 8*11.5 | SAMYOUNG(韩国三莹) | C165653 | LCSC
6 | 2 | SS14 | D1,D2 | SMA_L4.2-W2.6-LS5.3-RD |  | SS14 | MDD | C2480 | LCSC
7 | 1 | P6KE6.8A | D3 | DO-15_BD3.1-L6.7-P10.70-D0.9-RD |  | P6KE6.8A | Littelfuse(美国力特) | C409413 | LCSC
8 | 1 | MHK1560CRBTD | DS1 | LED-TH_MHK1560UGBTD |  | MHK1560CRBTD | MEIHUA(美华) | C7470835 | LCSC
9 | 1 | MHK1560UGBTD | DS2 | LED-TH_MHK1560UGBTD |  | MHK1560UGBTD | MEIHUA(美华) | C7470833 | LCSC
10 | 2 | Fuse Holder | F1,F2 | FUSE-TH_L24.5-W9.8-P22.5 |  | 保险丝透明座 | xcfuse(旭程) | C58066 | LCSC
11 | 2 | DBT50G-8.25-2P-BK-P | J1,J2 | CONN-TH_DBT50G-8.25-2P |  | DBT50G-8.25-2P-BK-P | DORABO(地博电气) | C918130 | LCSC
12 | 1 | T34001 | J3 | CONN-TH_T34001 |  | T34001 | XFCN(兴飞) | C481448 | LCSC
13 | 1 | D-SUB-DR-9PCM-CB | J4 | DB9-TH_ID09S33E4GV00LF |  | D-SUB-DR-9PCM-CB | XUNPU(讯普) | C19077337 | LCSC
14 | 1 | HF33F/005-HS3 | K1 | RELAYS-TH_HF33F-XX-HS1-XXX |  | HF33F/005-HS3 | HF(宏发) | C183618 | LCSC
15 | 1 | YDUU10.5-253L0321 | L1 | IND-TH_4P-L19.0-W17.0 |  | YDUU10.5-253L0321 | YJYCOIN(益嘉源) | C5200263 | LCSC
16 | 1 | 560uH | L2 | IND-TH_BD9.0-P5.00-D0.7 | 560uH | PK0810-561KB | SXN(顺翔诺) | C122800 | LCSC
17 | 4 | SMTSOM360BTR | MP1,MP2,MP3,MP4 | SMD_BD5.6-D4.1 |  | SMTSOM360BTR | YIYUAN(怡远) | C5221846 | LCSC
18 | 1 | D882 Y档160~320 | Q1 | SOT-89-3_L4.5-W2.5-P1.50-LS4.2-BR |  | D882 Y档160~320 | CJ(江苏长电/长晶) | C9634 | LCSC
19 | 4 | 1kΩ | R1,R2,R3,R4 | R0603 | 1kΩ | 0603WAF1001T5E | UNI-ROYAL(厚声) | C21190 | LCSC
20 | 2 | 5.1kΩ | R5,R6 | R0603 | 5.1kΩ | 0603WAF5101T5E | UNI-ROYAL(厚声) | C23186 | LCSC
21 | 1 | 10D471K | R7 | RES-TH_L12.5-W6.7-P7.50-D1.2 |  | 10D471K | RUILON(瑞隆源) | C8760 | LCSC
22 | 1 | DS18B20Z | U1 | SOP-8_L4.9-W3.9-P1.27-LS6.0-BL |  | DS18B20Z | UMW(友台半导体) | C695837 | LCSC
23 | 1 | MT9700 | U2 | SOT-23-5_L3.0-W1.7-P0.95-LS2.8-BR |  | MT9700 | 西安航天民芯 | C89855 | LCSC
24 | 1 | TAS10-5-W2 | U3 | PWRM-TH_TAS10-XX-W2 |  | TAS10-5-W2 | TDPOWER(腾达电源) | C2687655 | LCSC

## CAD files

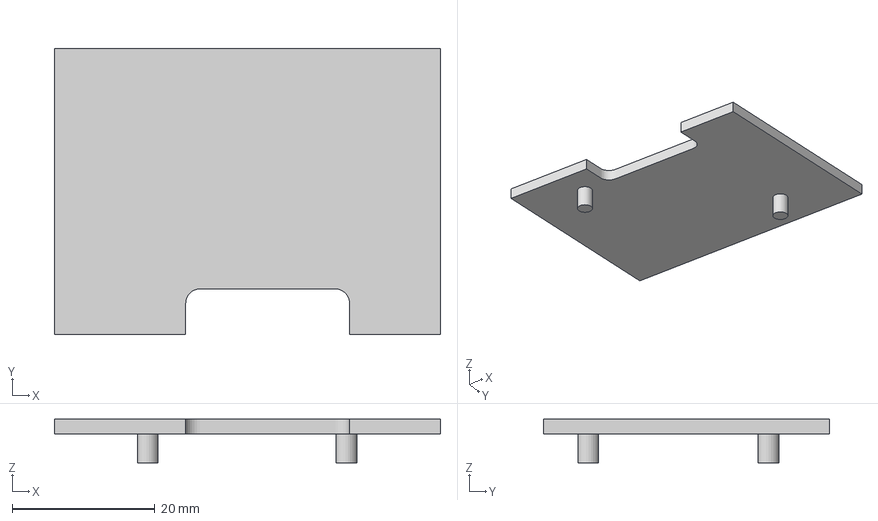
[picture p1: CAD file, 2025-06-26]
Core/2.3.2/Mechanical/3MF Files/Core NFC Spacer.3mf
54.0 x 40.1 x 6.10 mm

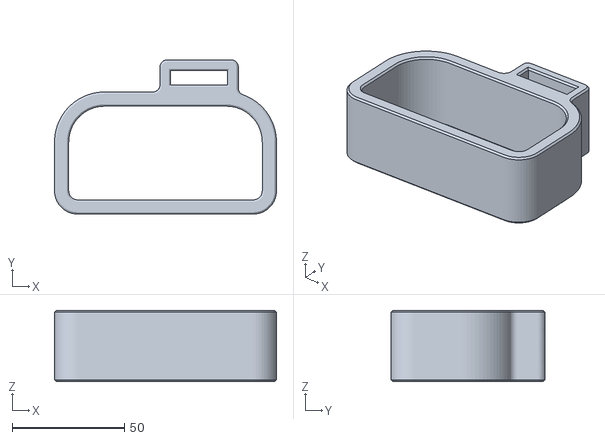
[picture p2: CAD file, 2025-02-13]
Switches/V2.X Switches/AC Power Switch/Mechanical/powerbox_mount_flat.stl
99.0 x 68.7 x 31.8

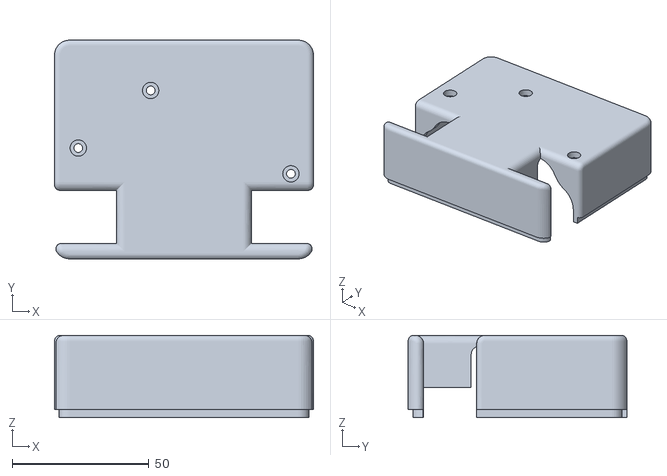
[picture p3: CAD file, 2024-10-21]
Switches/V2.X Switches/Contactor Switch/Mechanical/Case Top.stl
94.7 x 80.0 x 30.1

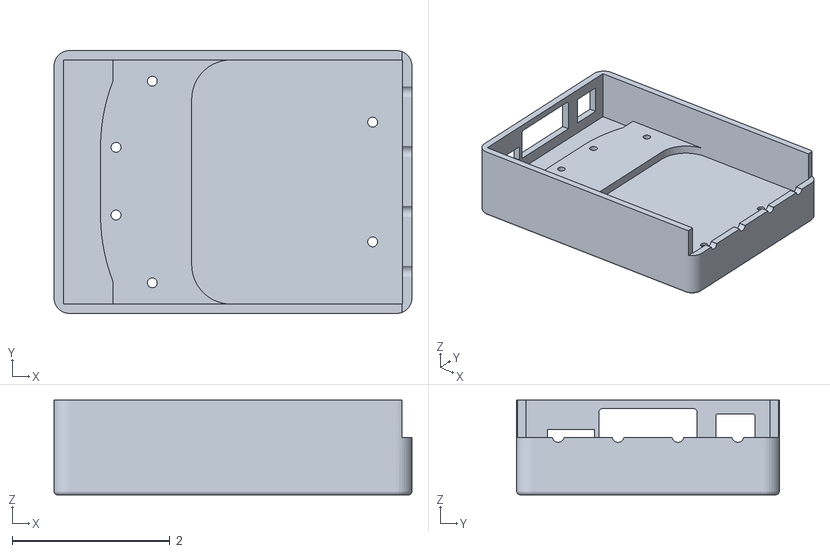
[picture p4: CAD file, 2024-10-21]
Switches/V2.X Switches/USB Hub Switch/Mechanical/USB Bottom.stl
4.54 x 3.34 x 1.21

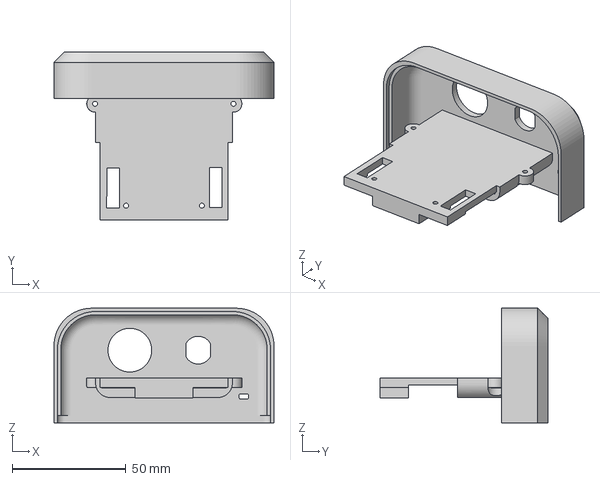
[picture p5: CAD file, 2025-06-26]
Core/2.3.2/Mechanical/3MF Files/Core Front Face.3mf
96.6 x 73.9 x 50.3 mm

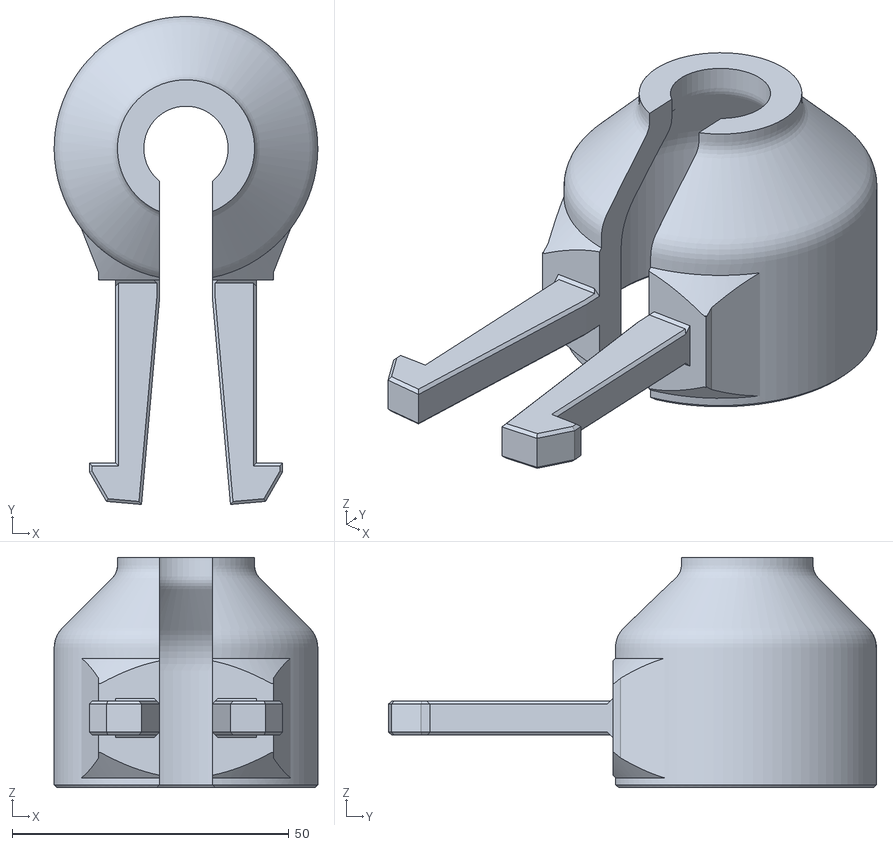
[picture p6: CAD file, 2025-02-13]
Switches/V2.X Switches/AC Power Switch/Mechanical/powerbox_plugkey.stl
47.6 x 88.1 x 41.6

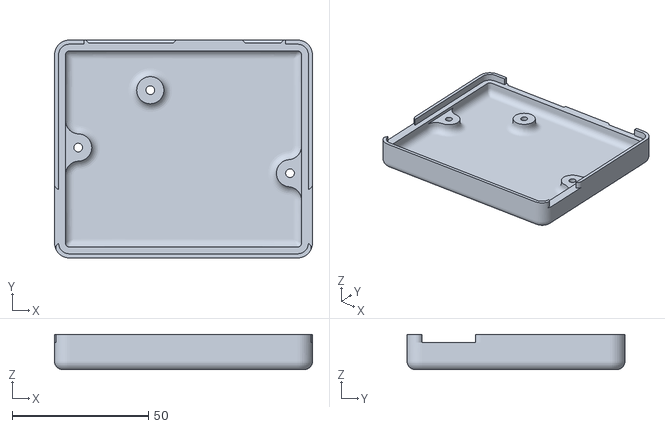
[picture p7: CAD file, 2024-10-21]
Switches/V2.X Switches/Contactor Switch/Mechanical/Case Bottom.stl
94.7 x 80.0 x 12.9

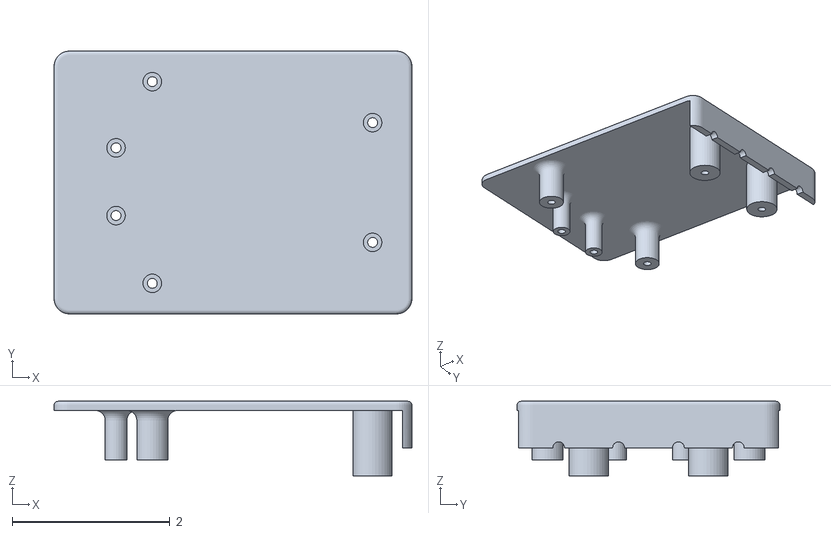
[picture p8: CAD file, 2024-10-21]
Switches/V2.X Switches/USB Hub Switch/Mechanical/USB Top.stl
4.54 x 3.34 x 0.946

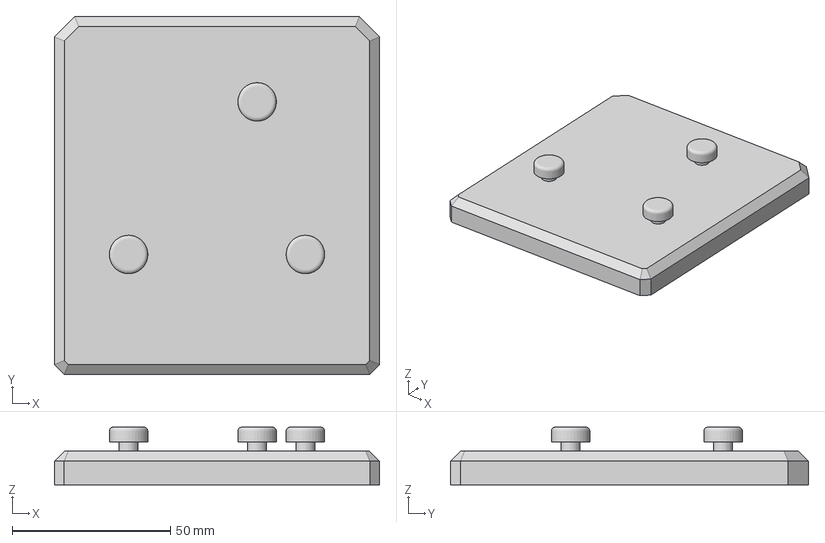
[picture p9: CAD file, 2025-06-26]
Core/2.3.2/Mechanical/3MF Files/Horizontal Mount.3mf
102.9 x 113.2 x 18.3 mm

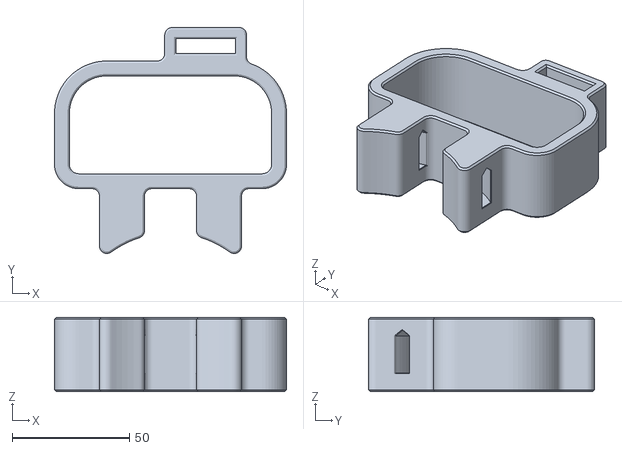
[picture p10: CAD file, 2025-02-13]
Switches/V2.X Switches/AC Power Switch/Mechanical/powerbox_mount_drillpress.stl
99.0 x 96.4 x 31.8

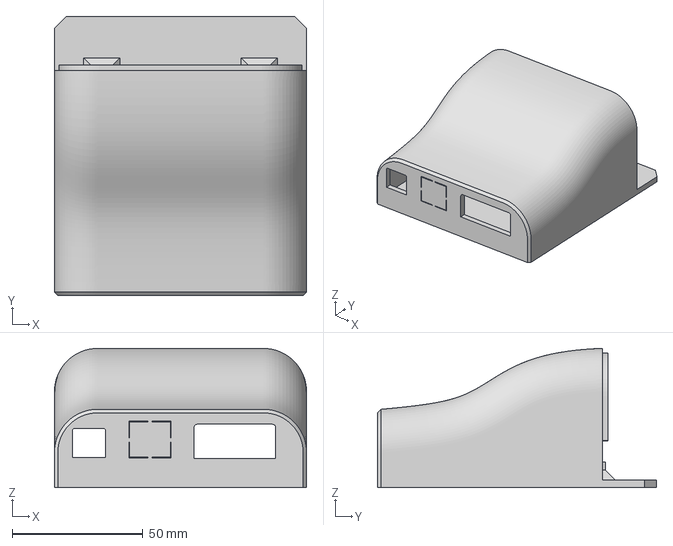
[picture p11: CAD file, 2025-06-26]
Core/2.3.2/Mechanical/3MF Files/Core Base.3mf
96.6 x 106.9 x 53.3 mm

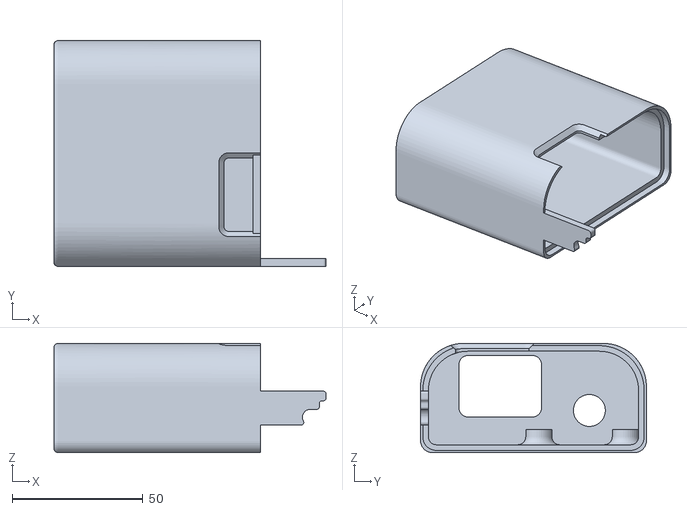
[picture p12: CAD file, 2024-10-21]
Switches/V2.X Switches/AC Power Switch/Mechanical/AC Case Left.stl
103.8 x 86.2 x 41.7

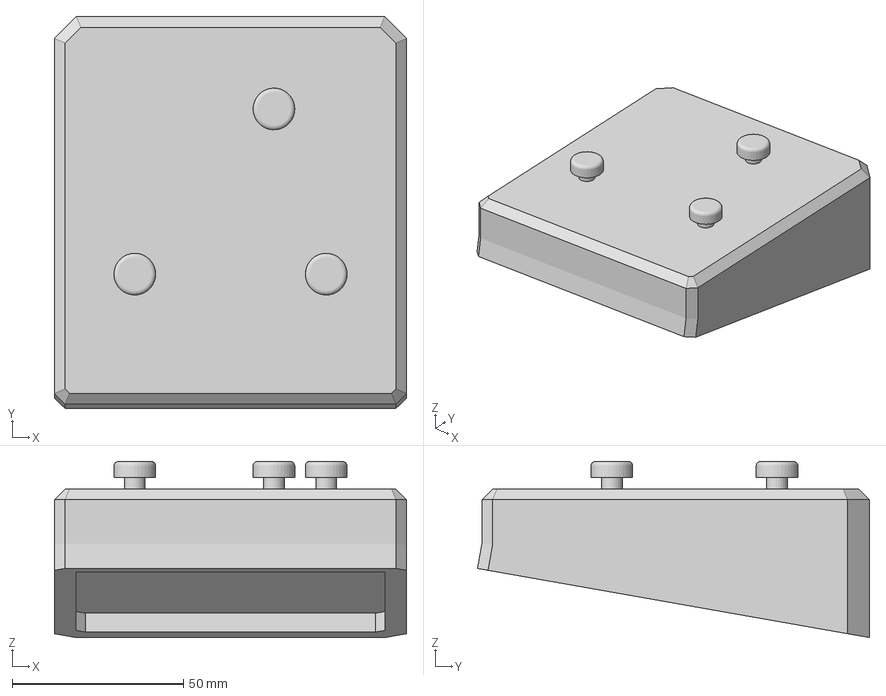
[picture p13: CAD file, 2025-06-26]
Core/2.3.2/Mechanical/3MF Files/10 Deg Mount.3mf
102.9 x 114.5 x 51.4 mm

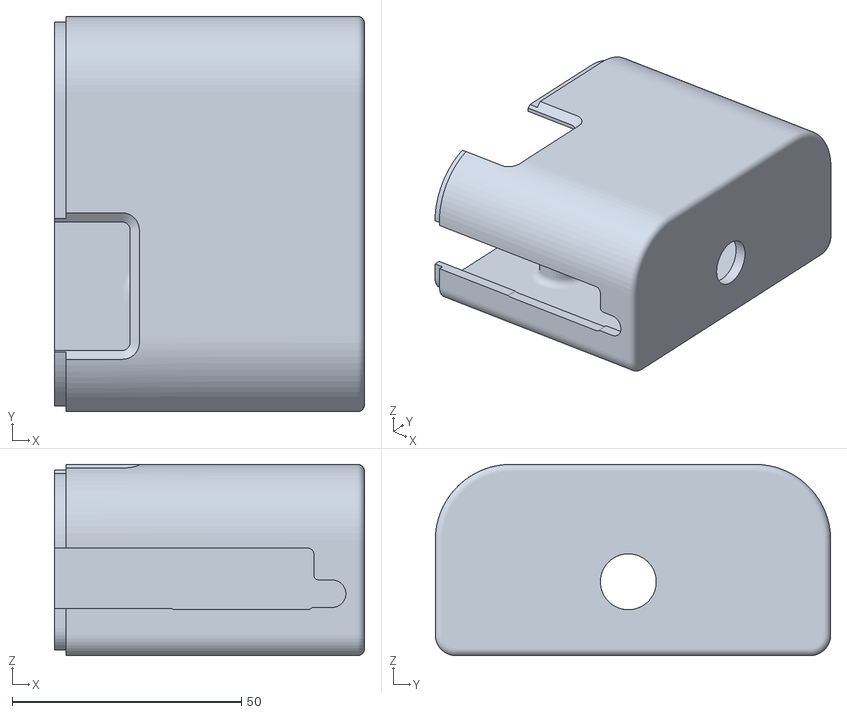
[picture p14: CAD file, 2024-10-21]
Switches/V2.X Switches/AC Power Switch/Mechanical/AC Case Right.stl
67.6 x 86.2 x 41.7

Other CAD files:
Switches/V2.X Switches/AC Power Switch/Mechanical/powerbox_mount_drillpress v1.f3d
Switches/V2.X Switches/AC Power Switch/Mechanical/powerbox_mount_flat v1.f3d
Switches/V2.X Switches/AC Power Switch/Mechanical/powerbox_plugkey v1.f3d
Switches/V2.X Switches/USB Hub Switch/Mechanical/USB Switch v7.f3z

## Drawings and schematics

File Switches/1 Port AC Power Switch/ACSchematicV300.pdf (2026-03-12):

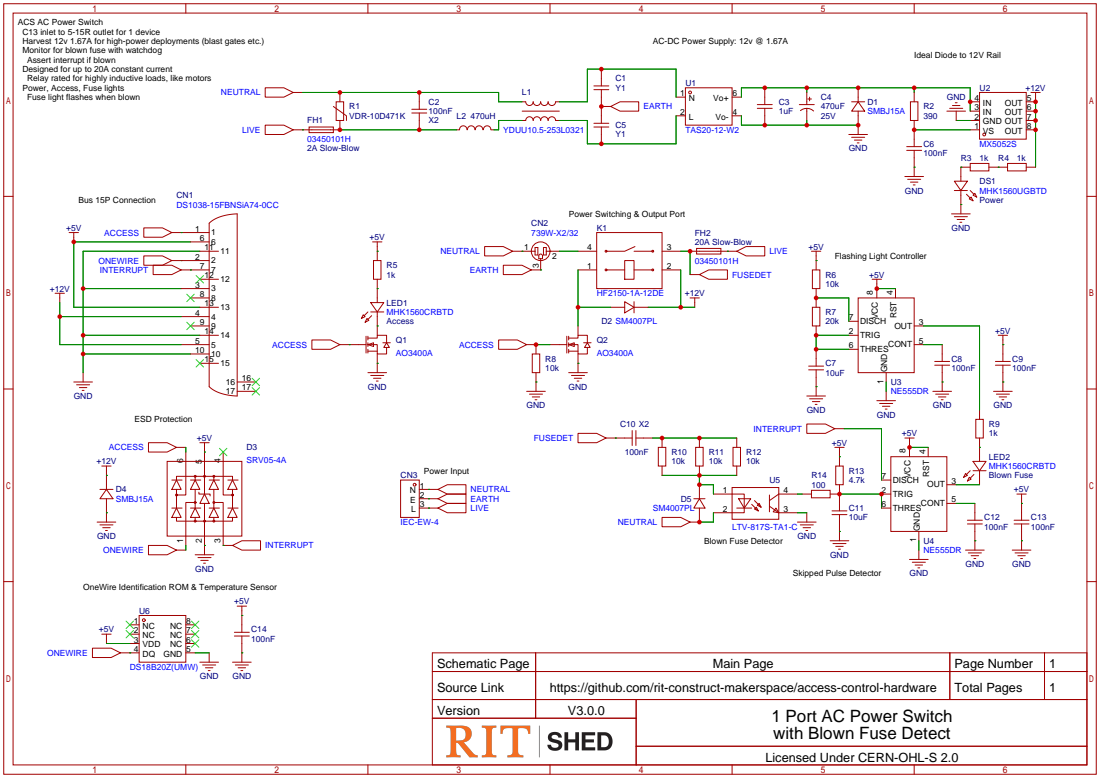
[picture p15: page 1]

ACS AC Power Switch
C13 inlet to 5-15R outlet for 1 device
Harvest 12v 1.67A for high-power deployments (blast gates etc.)
Monitor for blown fuse with watchdog
Assert interrupt if blown
Designed for up to 20A constant current
Relay rated for highly inductive loads, like motors
Power, Access, Fuse lights
Fuse light flashes when blown

AC-DC Power Supply: 12v @ 1.67A

Ideal Diode to 12V Rail

Power Switching & Output Port

OneWire Identification ROM & Temperature Sensor

Schematic Page | Main Page | Page Number | 1
Source Link | https://github.com/rit-construct-makerspace/access-control-hardware | Total Pages | 1

with Blown Fuse Detect

Licensed Under CERN-OHL-S 2.0

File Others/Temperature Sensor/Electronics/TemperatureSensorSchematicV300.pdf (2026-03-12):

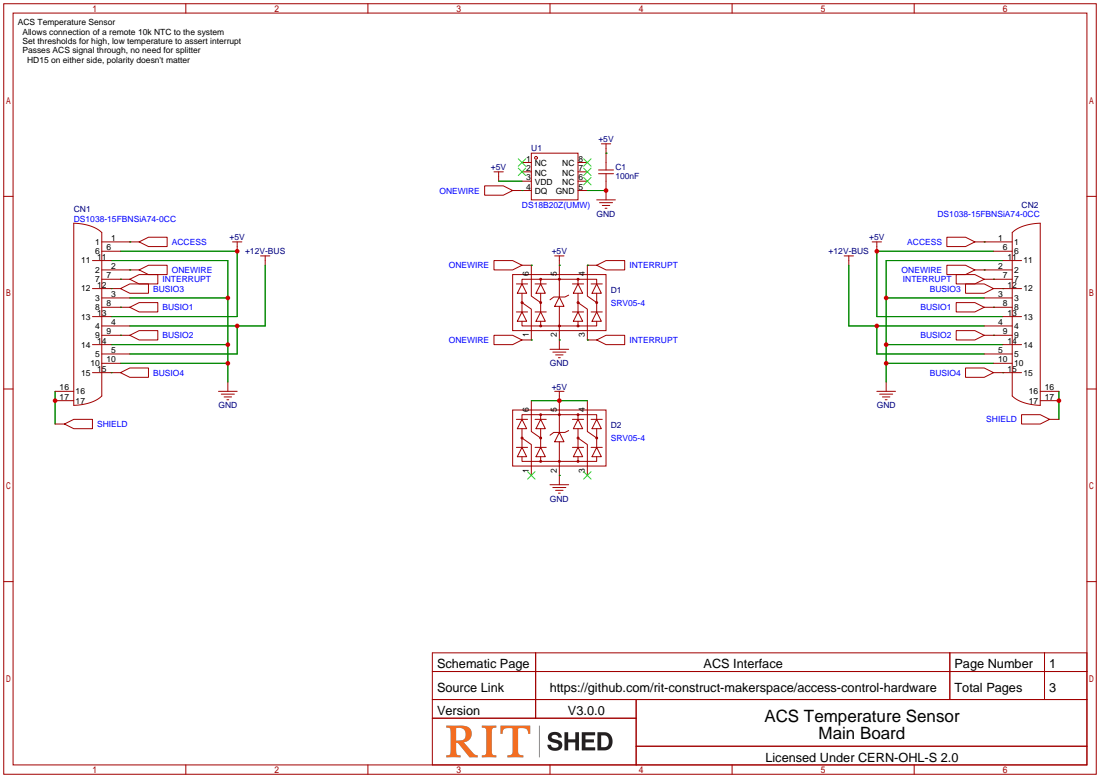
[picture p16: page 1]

ACS Temperature Sensor
Allows connection of a remote 10k NTC to the system
Set thresholds for high, low temperature to assert interrupt
Passes ACS signal through, no need for splitter
HD15 on either side, polarity doesn't matter

Schematic Page | ACS Interface | Page Number | 1
Source Link | https://github.com/rit-construct-makerspace/access-control-hardware | Total Pages | 3

Main Board

Licensed Under CERN-OHL-S 2.0

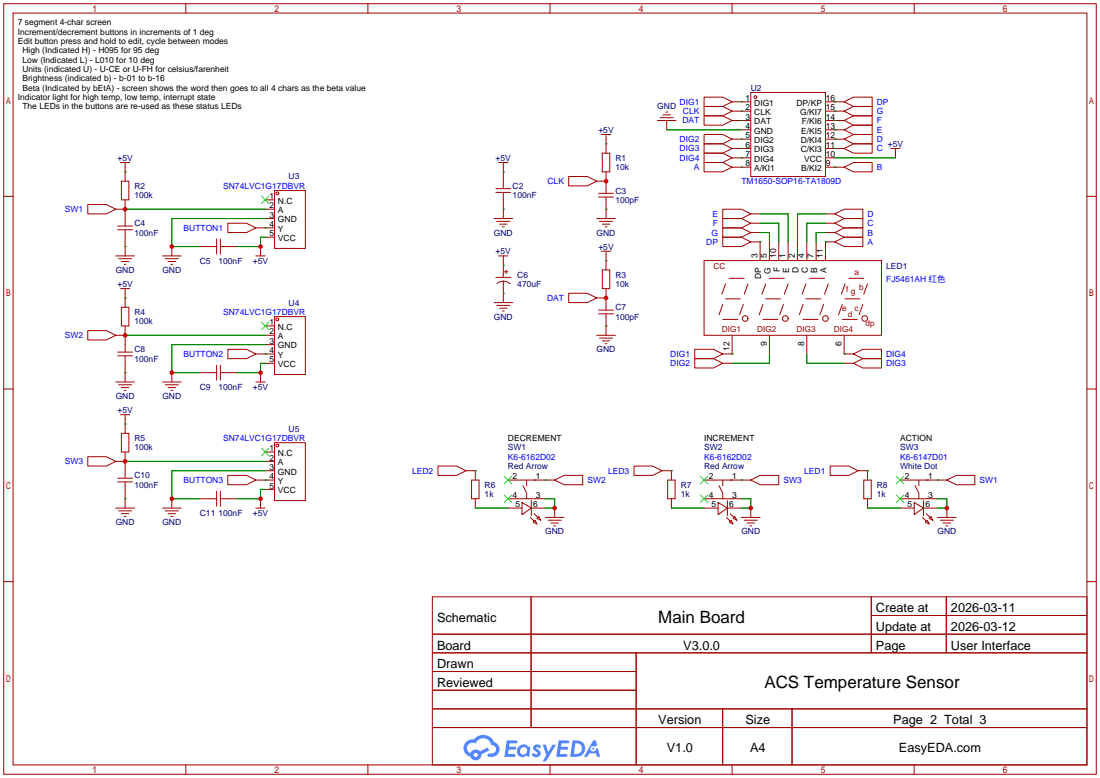
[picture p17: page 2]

7 segment 4-char screen
Increment/decrement buttons in increments of 1 deg
Edit button press and hold to edit, cycle between modes
High (Indicated H) - H095 for 95 deg
Low (Indicated L) - L010 for 10 deg
Units (indicated U) - U-CE or U-FH for celsius/farenheit
Brightness (indicated b) - b-01 to b-16
Beta (Indicated by bEtA) - screen shows the word then goes to all 4 chars as the beta value
The LEDs in the buttons are re-used as these status LEDs

Schematic | Main Board | Create at | 2026-03-11

Update at | 2026-03-12

Board | V3.0.0 | Page | User Interface
Drawn | | ACS Temperature Sensor
Reviewed

Version | Size | Page 2 Total 3
V1.0 | A4 | EasyEDA.com

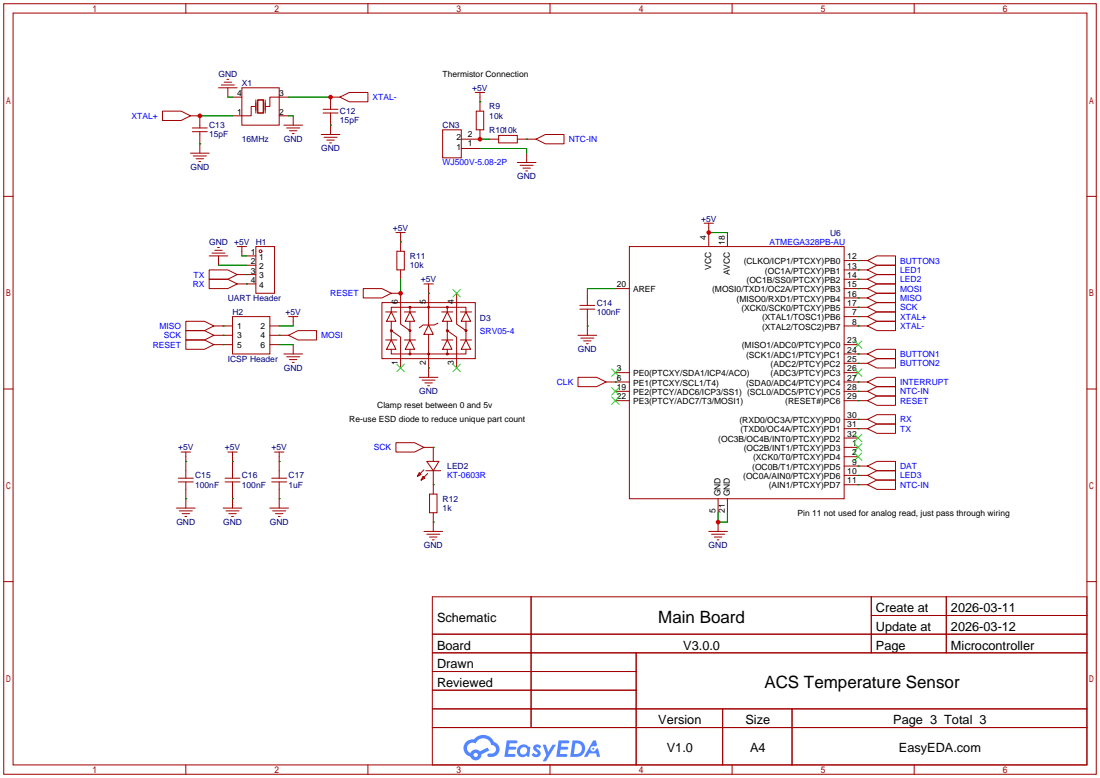
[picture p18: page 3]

Clamp reset between 0 and 5v
Re-use ESD diode to reduce unique part count

Pin 11 not used for analog read, just pass through wiring

Schematic | Main Board | Create at | 2026-03-11

Update at | 2026-03-12

Board | V3.0.0 | Page | Microcontroller
Drawn | | ACS Temperature Sensor
Reviewed

Version | Size | Page 3 Total 3
V1.0 | A4 | EasyEDA.com

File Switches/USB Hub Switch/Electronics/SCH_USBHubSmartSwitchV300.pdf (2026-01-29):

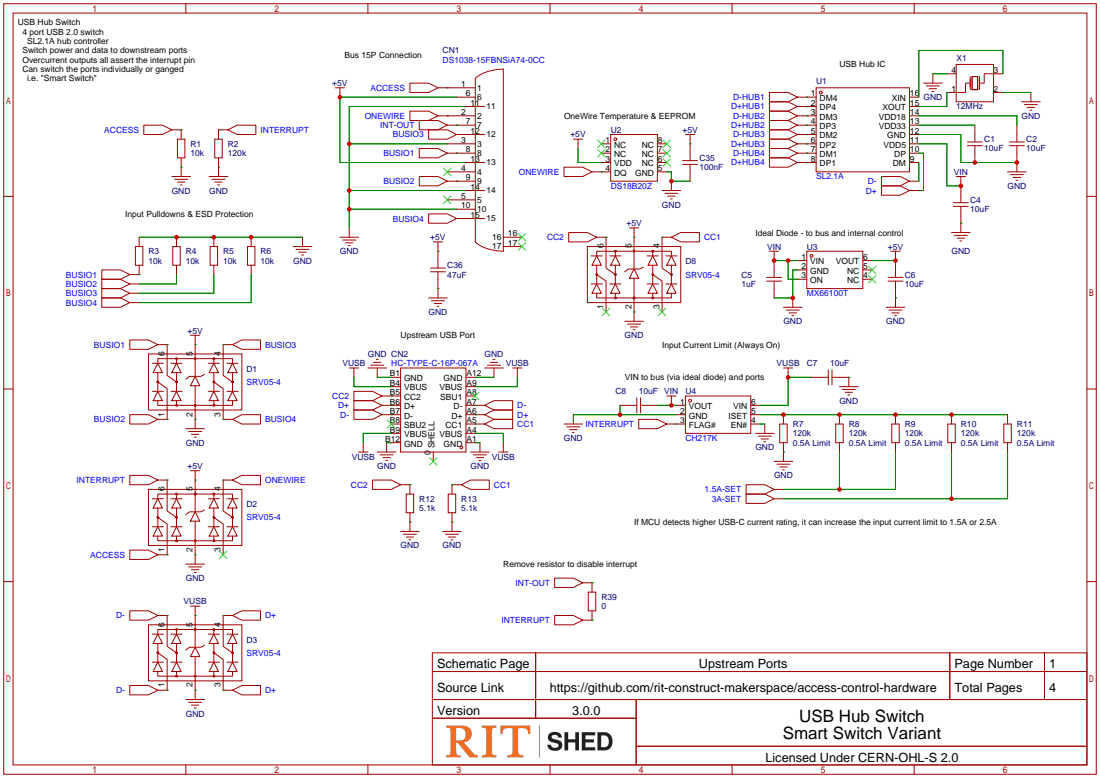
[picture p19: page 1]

USB Hub Switch
4 port USB 2.0 switch
SL2.1A hub controller
Switch power and data to downstream ports
Overcurrent outputs all assert the interrupt pin
Can switch the ports individually or ganged
i.e. "Smart Switch"

DP 10 VDD5 11 GND 12 VDD33 13 VDD18 14 XOUT 15 XIN 16

Input Pulldowns & ESD Protection

Ideal Diode - to bus and internal control
VIN

Input Current Limit (Always On)

VIN to bus (via ideal diode) and ports
C8 10uF VIN

If MCU detects higher USB-C current rating, it can increase the input current limit to 1.5A or 2.5A

Remove resistor to disable interrupt
INT-OUT

Schematic Page | Upstream Ports | Page Number | 1
Source Link | https://github.com/rit-construct-makerspace/access-control-hardware | Total Pages | 4

Smart Switch Variant

Licensed Under CERN-OHL-S 2.0

# GND 4 SH¹ SH²

# GND 4 SH¹ SH²

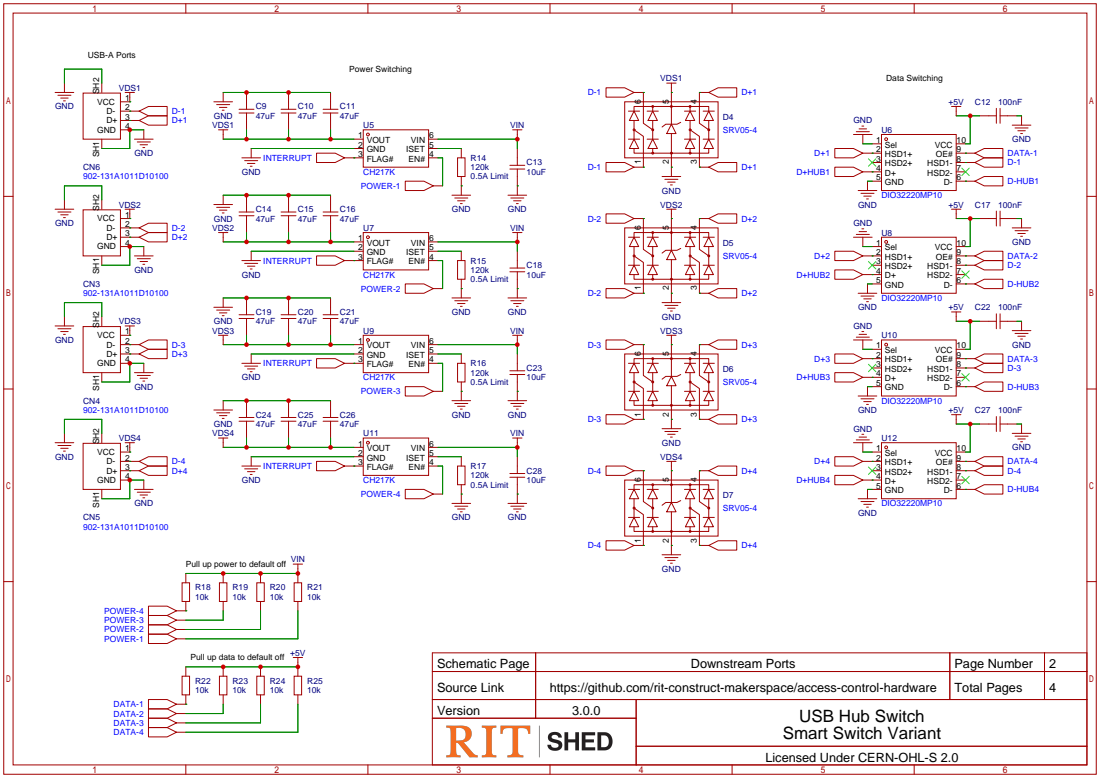
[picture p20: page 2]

Pull up power to default off

Pull up data to default off

Schematic Page | Downstream Ports | Page Number | 2
Source Link | https://github.com/rit-construct-makerspace/access-control-hardware | Total Pages | 4

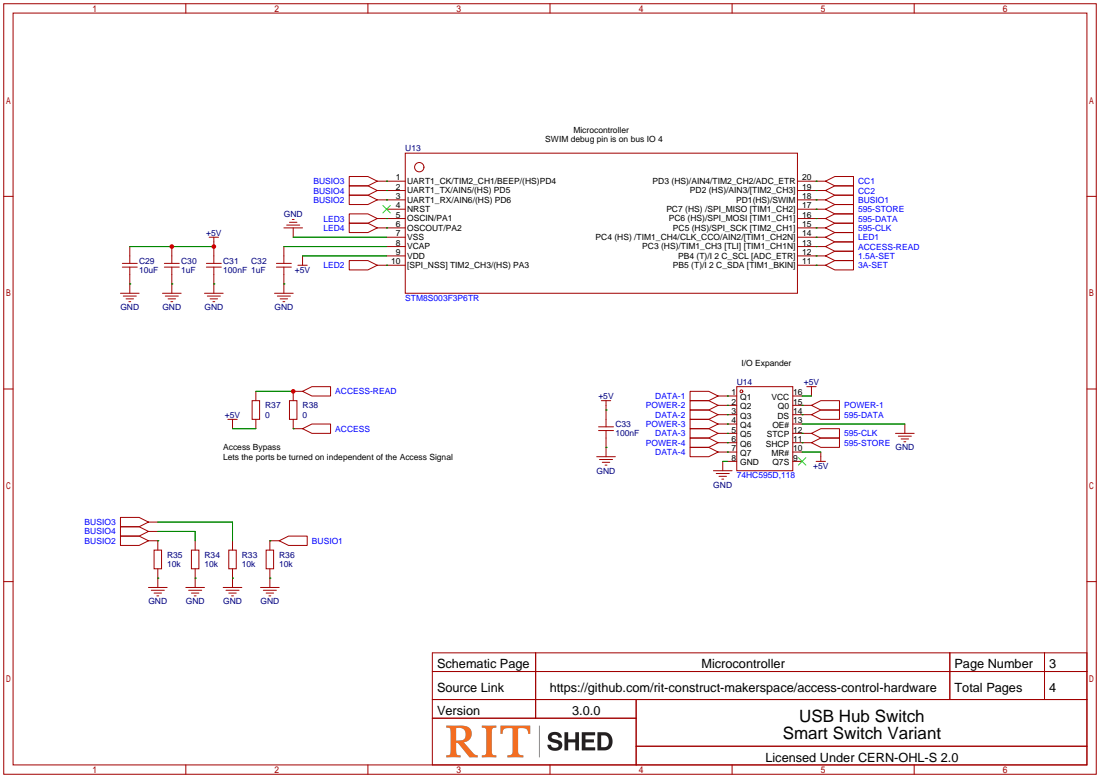
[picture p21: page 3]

Microcontroller
SWIM debug pin is on bus IO 4

MR# 10 SHCP 11 STCP 12 OE# 13 DS 14 Q0 15 VCC 16

Access Bypass
Lets the ports be turned on independent of the Access Signal

Schematic Page | Microcontroller | Page Number | 3
Source Link | https://github.com/rit-construct-makerspace/access-control-hardware | Total Pages | 4

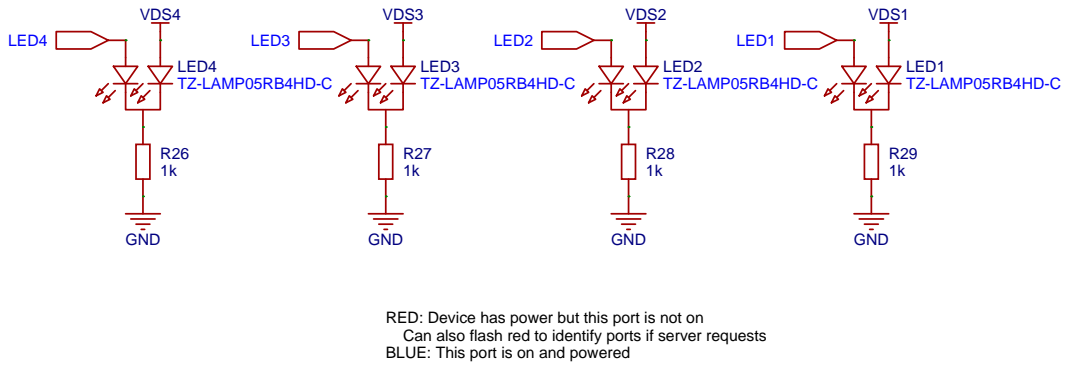
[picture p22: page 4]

RED: Device has power but this port is not on
Can also flash red to identify ports if server requests
BLUE: This port is on and powered

Schematic Page | Status LEDs | Page Number | 4
Source Link | https://github.com/rit-construct-makerspace/access-control-hardware | Total Pages | 4

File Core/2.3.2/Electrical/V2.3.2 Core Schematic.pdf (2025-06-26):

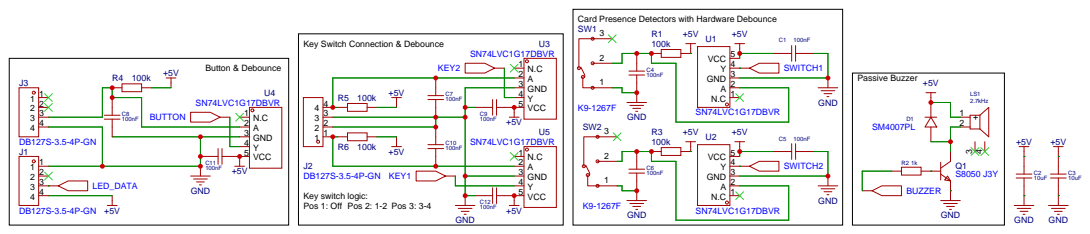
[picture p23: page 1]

Card Presence Detectors with Hardware Debounce

Key Switch Connection & Debounce

Key switch logic:
Pos 1: Off Pos 2: 1-2 Pos 3: 3-4

Schematic Page | Front End | Page Number | 1
Source Link | https://github.com/rit-construct-makerspace/access-control-hardware | Total Pages | 6

V2.3.2 Schematic

Licensed Under CERN-OHL-S 2.0

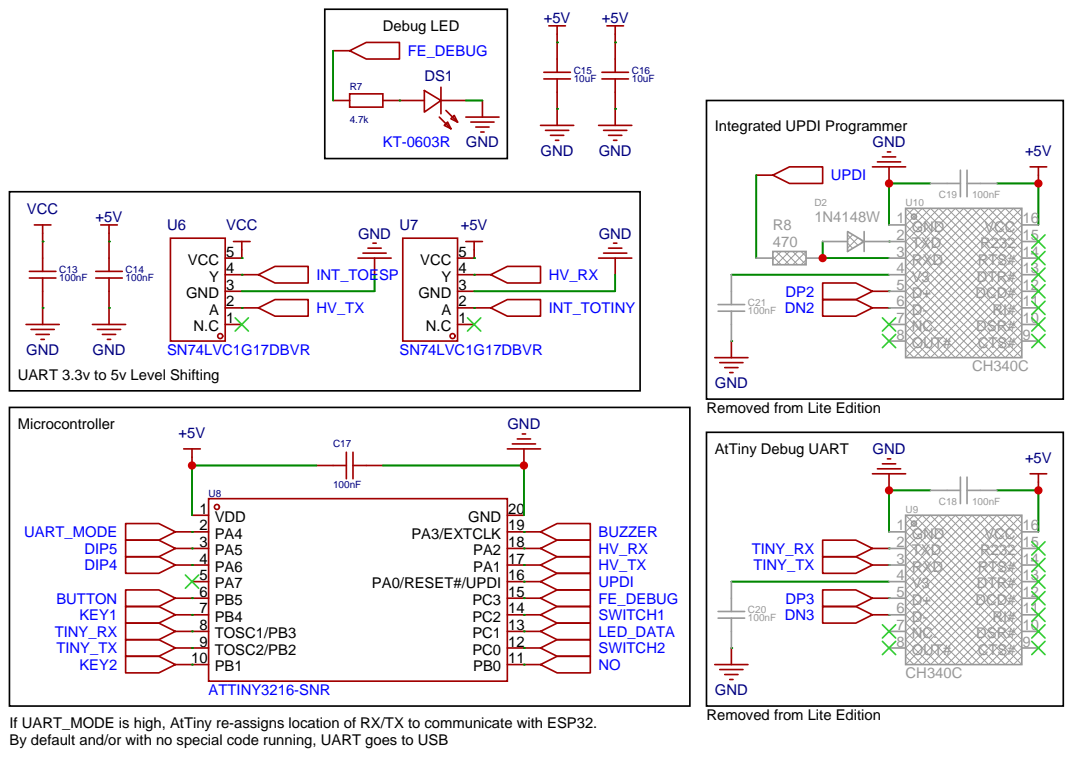
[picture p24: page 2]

UPDI
DSR# 10 RI# 11 DCD# 12 DTR# 13 RTS# 14 R232 15 VCC 16

GND
UART 3.3v to 5v Level Shifting

Removed from Lite Edition

If UART_MODE is high, AtTiny re-assigns location of RX/TX to communicate with ESP32.
By default and/or with no special code running, UART goes to USB

Schematic Page | Front End MCU | Page Number | 2
Source Link | https://github.com/rit-construct-makerspace/access-control-hardware | Total Pages | 6

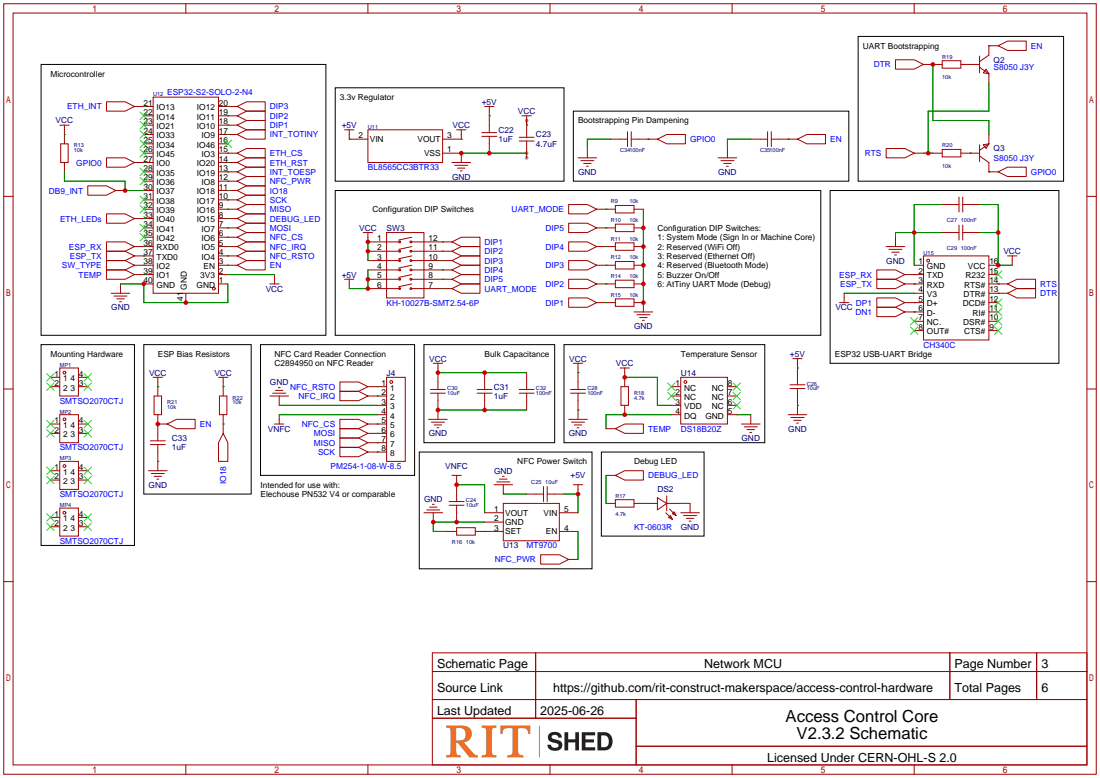
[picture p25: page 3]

Configuration DIP Switches:
1: System Mode (Sign In or Machine Core)
2: Reserved (WiFi Off)
3: Reserved (Ethernet Off)
4: Reserved (Bluetooth Mode)
5: Buzzer On/Off
6: AtTiny UART Mode (Debug)

DSR# 10 RI# 11 DCD# 12 DTR# 13 RTS# 14 R232 15 VCC 16

Intended for use with:
Elechouse PN532 V4 or comparable

Schematic Page | Network MCU | Page Number | 3
Source Link | https://github.com/rit-construct-makerspace/access-control-hardware | Total Pages | 6

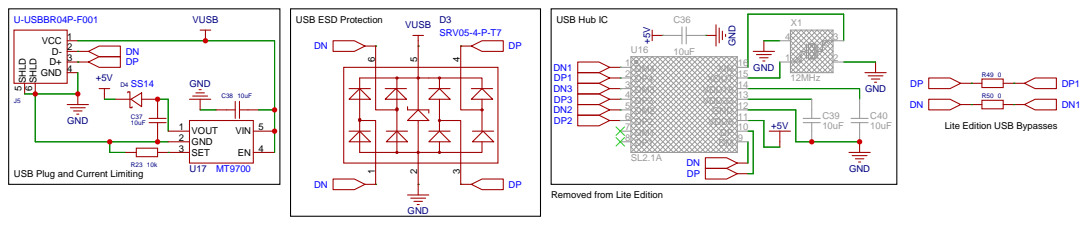
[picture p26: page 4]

DP 10 VDD5 11 GND 12 VDD33 13 VDD18 14 XOUT 15 XIN 16

Lite Edition USB Bypasses

USB Plug and Current Limiting

Removed from Lite Edition

Schematic Page | USB | Page Number | 4
Source Link | https://github.com/rit-construct-makerspace/access-control-hardware | Total Pages | 6


Schematic Page | Switch Interface | Page Number | 5
Source Link | https://github.com/rit-construct-makerspace/access-control-hardware | Total Pages | 6


Ethernet hardware is not present in the Lite edition ACS Core

Schematic Page | Ethernet | Page Number | 6
Source Link | https://github.com/rit-construct-makerspace/access-control-hardware | Total Pages | 6

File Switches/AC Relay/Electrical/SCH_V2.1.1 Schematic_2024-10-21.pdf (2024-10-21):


AC to 12V Power Module

VRAW AC Relay and Relay Driver

Access Control AC Power Switch

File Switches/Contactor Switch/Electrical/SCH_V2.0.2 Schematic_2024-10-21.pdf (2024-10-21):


AC to 5V Power Module

Access Control Contactor Switch

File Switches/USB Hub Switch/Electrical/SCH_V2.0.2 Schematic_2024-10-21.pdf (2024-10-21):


Switch Connector and CBI LEDs

DP 10 VDD5 11 GND 12 VDD33 13 VDD18 14 XOUT 15 XIN 16

Bulk Capacitance >100uF per port

Access Control USB Hub Switch

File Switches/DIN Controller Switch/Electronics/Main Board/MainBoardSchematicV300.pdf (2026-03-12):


ACS DIN Controller
DIN rail mounted ACS switch controller
Designed to fit in BUD DMB-4773 DIN enclosure
Top board shows ACS state on front faceplate
Main board (this one) has power regulation, switching, IO
12v 1.67A regulator - 250V input
Auxiliary 12v input if system already has regulator
Auxiliary Interrupt input active high 3.3-12v (3mA at 12v)
NO-COM-NC set for each IO&Access, one for just Access
250VAC at 2A
15 pin ACS interface on screw terminals for easier routing

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

Main Board

Licensed Under CERN-OHL-S 2.0

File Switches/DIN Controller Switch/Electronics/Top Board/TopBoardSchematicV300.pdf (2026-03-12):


ACS DIN Controller
DIN rail mounted ACS switch controller
Designed to fit in BUD DMB-4773 DIN enclosure
Main board has power regulation, switching, IO
Top board (this one) shows ACS state on front faceplate

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

Top Board

Licensed Under CERN-OHL-S 2.0

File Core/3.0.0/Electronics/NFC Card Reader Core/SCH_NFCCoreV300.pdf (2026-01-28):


ANT1 is inherent to the PCB

Schematic Page | NFC Reader | Page Number | 1
Source Link | https://github.com/rit-construct-makerspace/access-control-hardware | Total Pages | 7

NFC Card Reader

Licensed Under CERN-OHL-S 2.0


Generic Screen/Expansion Interface

Tamper detection, screen auto-orientation

ESD Protection (Flow-Through Wiring)

USB Current Limiting, Reverse Current Blocking

Schematic Page | Interfaces | Page Number | 2
Source Link | https://github.com/rit-construct-makerspace/access-control-hardware | Total Pages | 7


JK-nSMD100-16
1A Hold, 1.8A Trip Self-Healing Fuse

Default: Bus GPIO are inputs

Schematic Page | Bus Connection | Page Number | 3
Source Link | https://github.com/rit-construct-makerspace/access-control-hardware | Total Pages | 7


Runs on 12v or 5v, whichever is present

12v -> 5v 1A Regulator
Ideal diode output to bus

Schematic Page | Regulators | Page Number | 4
Source Link | https://github.com/rit-construct-makerspace/access-control-hardware | Total Pages | 7


MISO Tri-State Buffer

Schematic Page | Ethernet | Page Number | 5
Source Link | https://github.com/rit-construct-makerspace/access-control-hardware | Total Pages | 7


UART Header
Debug or generic expansion

Schematic Page | Microcontroller | Page Number | 6
Source Link | https://github.com/rit-construct-makerspace/access-control-hardware | Total Pages | 7


The Card Slot hardware can be easily repurposed as hardware for a Tap Pad
To convert from a card slot to a tap pad:
Move jumper resistors
Move RGB LED to LED2 position
Replace side-fire buzzer with top-fire

This is how the MCU knows to act as a tap pad.
HIGH: Card slot
LOW: Tap pad

This improves visibility, with the light facing towards the user.

This improves sound percetion, since it will fire directly towards the user.

Schematic Page | Tap Variant | Page Number | 7
Source Link | https://github.com/rit-construct-makerspace/access-control-hardware | Total Pages | 7

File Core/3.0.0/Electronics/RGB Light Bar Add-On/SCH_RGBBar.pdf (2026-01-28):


ACS Core - Light Bar
Simple RGB Light Bar
Connects via standard IDC header
Gives a bit more info than the single RGB LED, but is not as expensive/large as a screen

OneWire EEPROM/Temp Sensor

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

RGB Light Bar Add-On

Licensed Under CERN-OHL-S 2.0

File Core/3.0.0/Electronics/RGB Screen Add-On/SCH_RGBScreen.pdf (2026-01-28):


Access Control Core - RGB Screen
Screen daughterboard based on NHD 128x64 RGB COG Screen
NHD-C12864DA-FSRGB-FBW-3V3
NHD-C12864DA-FSW-FBW-3V3
Standard wire interface for other screens
Exposes 6 raw GPIO, no designated assignments
Allows for SPI, i2C, or UART based on what's needed
5v, 3.3v rails
Onewire connection for EEPROM
Tells Core how to treat the IO, what kind of screen, etc.

OneWire EEPROM/Temp Sensor

3V LDO (Screen Nominal Voltage)

Schematic Page | Interfaces | Page Number | 1
Source Link | https://github.com/rit-construct-makerspace/access-control-hardware | Total Pages | 3

RGB Screen Add-On

Licensed Under CERN-OHL-S 2.0


Green Cathode or Anode
For RGB vs White Backlight
VANODE

When running a screen with white backlight,
RED Cathode becomes the backlight cathode.

Schematic Page | Backlighting | Page Number | 2
Source Link | https://github.com/rit-construct-makerspace/access-control-hardware | Total Pages | 3

# 4Y 10 5A 11 5Y 12 N.C/2 13 6A 14 6Y 15 N.C 16


Set Serial SPI Mode

Schematic Page | Screen | Page Number | 3
Source Link | https://github.com/rit-construct-makerspace/access-control-hardware | Total Pages | 3

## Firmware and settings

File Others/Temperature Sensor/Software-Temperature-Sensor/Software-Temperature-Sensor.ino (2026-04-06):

/*

ACS Temperature Sensor

This add-on to the ACS bus will monitor a remote 10k thermistor, and report over- and under-temperature concerns via the interrupt pin. 

Onboard 3-key interface allows you to set information about the system. 

Settings:
  Enter settings by pressing and holding center button for 3 seconds, when Acces signal is not on.
  When in settings menu, center button flashes every 500mS
  Following settings available:
    Units (Indicated U) - U-CE or U-FH for Celsius/Farenheit
    High Temperature (Indicated H) - H095 for 95 degrees
    Low (Incidated L) - L010 for 10 degrees
    Brightness (indicated b) - bOFF for 0, b-01 to b-07 for 0-7. Should update in real-time to show, except 0 which is shown as 1. 
    Beta (indicated by bEtA) - screen shows the word, then flashes to the value as all 4 chars.
  Once you cycle through all settings, return to normal operation.

Display:
   Shows current temperature with unit when running
   When over- or under-temperature event, flash the accompanying button's light

*/

//Libraries
#include <TM16xx.h>
#include <TM1650.h>
#include <TM16xxDisplay.h>
#include <EEPROM.h>

//Pin Definitions
const byte THERM_PIN = PIN_PC5; 
const byte DAT_PIN = PIN_PD5;
const byte UP_LED = PIN_PD6;  //LED3
const byte UP_BUTTON = PIN_PB0; //Button3
const byte SET_LED = PIN_PB1; //LED1
const byte SET_BUTTON = PIN_PC1; //Button 1
const byte DOWN_LED = PIN_PB2; //LED2
const byte DOWN_BUTTON = PIN_PC2; //Button 2
const byte INTERRUPT_PIN = PIN_PC4;
const byte CLK_PIN = PIN_PE1;

//Global Variables - Settings
bool isCelsius = true;   // true = U-CE, false = U-FH
int highTemp = 95;       // H095
int lowTemp = 10;        // L010
int brightness = 7;      // 0 = bOFF, 1-7 = b-01 to b-07
int betaValue = 3950;    // Alternates bEtA / 3950

//Global Variables - Other
unsigned long ButtonTime = 0;
unsigned long lastTempReadTime = 0;
unsigned long lastAlarmBlinkTime = 0;
bool alarmBlinkState = false;
float currentTemp = 0.0;
bool isAlarming = false;
byte activeAlarmType = 0; // 0=None, 1=High, 2=Low
float smoothedTemp = -999.0; // -999.0 indicates uninitialized

//Objects
TM1650 chip(DAT_PIN, CLK_PIN);
TM16xxDisplay display(&chip, 4);

void setup() {
  // put your setup code here, to run once:

  //Step 1: Load Old Settings
  //First 4 bytes kept empty for future use
  EEPROM.get(4, highTemp);     // Bytes 4, 5
  EEPROM.get(6, lowTemp);      // Bytes 6, 7
  EEPROM.get(8, isCelsius);    // Byte 8
  EEPROM.get(9, brightness);   // Bytes 9, 10
  EEPROM.get(11, betaValue);   // Bytes 11, 12

if (betaValue < 1000 || betaValue > 5000) {
    // Memory is invalid, apply defaults
    isCelsius = true;
    highTemp = 85;
    lowTemp = 10;
    brightness = 7;
    betaValue = 3950;
  }

  //Set the screen brightness from memory
  display.setIntensity(brightness);

  //PinModes
  pinMode(SET_LED, OUTPUT);
  pinMode(UP_LED, OUTPUT);
  pinMode(DOWN_LED, OUTPUT);
  
  //Initial write of the interrupt to set open-drain mode. 
  digitalWrite(INTERRUPT_PIN, LOW);

}

void loop() {
  unsigned long currentMillis = millis();

  // --- Static timing variables for the loop ---
  static unsigned long lastTempReadTime = 0;
  static unsigned long lastAlarmBlinkTime = 0;
  static unsigned long lastDisplayUpdate = 0;
  
  static bool alarmBlinkState = false;
  static bool showAlarmText = false;
  
  static float currentTemp = 0.0;
  static bool isAlarming = false;
  static byte activeAlarmType = 0; // 0=None, 1=High, 2=Low, 3=Hardware Error
  static bool ntcError = false;

  // ---------------------------------------------------------
  // Step 1: Read and Smooth the Temperature (10Hz)
  // ---------------------------------------------------------
  if (currentMillis - lastTempReadTime >= 100) {
    lastTempReadTime = currentMillis;

    int rawADC = analogRead(THERM_PIN);
    
    // Check for Open Circuit (~1023) or Short Circuit (~0)
    if (rawADC > 1015 || rawADC < 5) {
      ntcError = true;
    } else {
      ntcError = false;
      
      // Calculate Resistance (thermistor to Ground, 10k to 5V)
      float resistance = 10000.0 / ((1023.0 / (float)rawADC) - 1.0);

      // Steinhart-Hart Equation
      float steinhart = resistance / 10000.0;       
      steinhart = log(steinhart);                   
      steinhart /= (float)betaValue;                
      steinhart += 1.0 / (25.0 + 273.15);           
      steinhart = 1.0 / steinhart;                  
      steinhart -= 273.15;                          

      float newTemp = isCelsius ? steinhart : (steinhart * 9.0 / 5.0) + 32.0;

      // Apply Exponential Moving Average (EMA) Filter
      if (smoothedTemp == -999.0) {
        smoothedTemp = newTemp; // Snap to value on first boot
      } else {
        smoothedTemp = (smoothedTemp * 0.8) + (newTemp * 0.2); 
      }
      currentTemp = smoothedTemp;
    }
  }

  // ---------------------------------------------------------
  // Step 2: Check Alarms
  // ---------------------------------------------------------
  if (ntcError) {
    isAlarming = true;
    activeAlarmType = 3; // NTC Hardware Error
  } else if (currentTemp >= highTemp) {
    isAlarming = true;
    activeAlarmType = 1; // High Alarm
  } else if (currentTemp <= lowTemp) {
    isAlarming = true;
    activeAlarmType = 2; // Low Alarm
  } else {
    isAlarming = false;
    activeAlarmType = 0;
    digitalWrite(UP_LED, LOW);
    digitalWrite(DOWN_LED, LOW);
  }

  if(isAlarming){
    pinMode(INTERRUPT_PIN, OUTPUT);
  } else{
    pinMode(INTERRUPT_PIN, INPUT);
  }

  // ---------------------------------------------------------
  // Step 3: Fast Alarm LED Flashing (4Hz)
  // ---------------------------------------------------------
  if (isAlarming) {
    if (currentMillis - lastAlarmBlinkTime >= 250) { 
      lastAlarmBlinkTime = currentMillis;
      alarmBlinkState = !alarmBlinkState;

      if (activeAlarmType == 1) { 
        digitalWrite(UP_LED, alarmBlinkState ? HIGH : LOW);
        digitalWrite(DOWN_LED, LOW);
      } else if (activeAlarmType == 2) { 
        digitalWrite(DOWN_LED, alarmBlinkState ? HIGH : LOW);
        digitalWrite(UP_LED, LOW);
      } else if (activeAlarmType == 3) {
        // Flash BOTH LEDs for a hardware error
        digitalWrite(UP_LED, alarmBlinkState ? HIGH : LOW);
        digitalWrite(DOWN_LED, alarmBlinkState ? HIGH : LOW);
      }
    }
  }

  // ---------------------------------------------------------
  // Step 4: Display Formatting & Updating (2Hz)
  // ---------------------------------------------------------
  if (currentMillis - lastDisplayUpdate >= 500) {
    lastDisplayUpdate = currentMillis;

    // --- User's Brightness Override ---
    // Update the screen intensity here so we don't flood the data bus
    int activeBrt = brightness;
    if (isAlarming && brightness == 0) {
      activeBrt = 1;
    }
    display.setIntensity(activeBrt);

    // Build the Temperature String
    char tempStr[6];
    char unit = isCelsius ? 'C' : 'F';

    // Format the temperature text
    if (currentTemp <= -10.0 || currentTemp >= 100.0) {
      int tempInt = (int)(currentTemp > 0 ? currentTemp + 0.5 : currentTemp - 0.5); 
      snprintf(tempStr, sizeof(tempStr), "%3d%c", tempInt, unit);
    } else {
      char floatBuf[6];
      dtostrf(currentTemp, 1, 1, floatBuf); 
      if (currentTemp >= 0.0 && currentTemp < 10.0) {
        snprintf(tempStr, sizeof(tempStr), " %s%c", floatBuf, unit);
      } else {
        snprintf(tempStr, sizeof(tempStr), "%s%c", floatBuf, unit);
      }
    }

    // Push to Screen
    if (isAlarming) {
      showAlarmText = !showAlarmText; 
      if (showAlarmText) {
        if (activeAlarmType == 1) display.println(" HI ");
        else if (activeAlarmType == 2) display.println(" LO ");
        else if (activeAlarmType == 3) display.println("NTC ");
      } else {
        if (activeAlarmType == 3) display.println(" ERR");
        else display.println(tempStr);
      }
    } else {
      showAlarmText = false; 
      display.println(tempStr);
    }
  }

  // ---------------------------------------------------------
  // Step 5: Settings Menu Entry & Standby Breathing Logic
  // ---------------------------------------------------------
  if (digitalRead(SET_BUTTON) == HIGH) { // Button is NOT pressed
    ButtonTime = currentMillis + 3000;
    
    // Breathing LED (Only if user set brightness to 0 AND no alarms are active)
    if (brightness == 0 && !isAlarming) {
      // Create a continuous 4000 millisecond (4 second) cycle
      unsigned long breathCycle = currentMillis % 4000; 
      int fadeValue;
      
      if (breathCycle < 2000) {
        // First 2 seconds: Fade In (Map 0-1999ms to PWM 0-255)
        fadeValue = map(breathCycle, 0, 1999, 0, 255);
      } else {
        // Next 2 seconds: Fade Out (Map 2000-3999ms to PWM 255-0)
        fadeValue = map(breathCycle, 2000, 3999, 255, 0);
      }
      
      analogWrite(SET_LED, fadeValue);
    } else {
      // Screen is on (normal operation or alarm mode), turn LED off
      digitalWrite(SET_LED, LOW);
    }
    
  } else { // Button IS pressed
    digitalWrite(SET_LED, HIGH); // Force solid ON so user knows they are pressing it
    
    if (currentMillis >= ButtonTime) {
      display.println("CONF");
      delay(1000);
      runSettingsMenu();
      
      // Reset timers so it reads immediately upon exit
      lastTempReadTime = 0; 
      lastDisplayUpdate = 0;
      ButtonTime = millis() + 3000; 
    }
  }
}

void runSettingsMenu() {
  bool inMenu = true;
  int menuState = 0; // 0:Units, 1:High, 2:Low, 3:Brightness, 4:Beta
  
  unsigned long previousBlinkMillis = 0;
  bool blinkState = true; 
  unsigned long lastInteractionMillis = millis();
  
  bool lastSet = HIGH, lastUp = HIGH, lastDown = HIGH;

  // Press-and-Hold Timing Variables
  unsigned long upPressTime = 0, upRepeatTime = 0;
  unsigned long downPressTime = 0, downRepeatTime = 0;
  
  // --- NEW: Acceleration Variables ---
  const unsigned long HOLD_DELAY = 500;         // Wait 500ms before auto-scrolling
  const unsigned long START_REPEAT_RATE = 150;  // Start slow (150ms per tick)
  const unsigned long MIN_REPEAT_RATE = 15;     // Max speed floor (15ms per tick)
  const unsigned long RATE_ACCELERATION = 10;   // Speed up by 10ms every tick
  
  unsigned long currentUpRate = START_REPEAT_RATE;
  unsigned long currentDownRate = START_REPEAT_RATE;

  // Force screen on to start the menu
  int activeBrt = (brightness == 0) ? 1 : brightness;
  display.setIntensity(activeBrt);

  while (inMenu) {
    unsigned long currentMillis = millis();

    // 1. Check Idle Timeout (10 seconds)
    if (currentMillis - lastInteractionMillis >= 10000) {
      inMenu = false;
      break; 
    }

    // Read Buttons
    bool currentSet  = digitalRead(SET_BUTTON);
    bool currentUp   = digitalRead(UP_BUTTON);
    bool currentDown = digitalRead(DOWN_BUTTON);

    // Pause Blinking While Holding Any Button
    if (currentSet == LOW || currentUp == LOW || currentDown == LOW) {
      previousBlinkMillis = currentMillis;
      blinkState = true; 
    }

    // ---------------------------------------------------------
    // 2. SET BUTTON (Single Click Only)
    // ---------------------------------------------------------
    if (currentSet == LOW && lastSet == HIGH) {
      lastInteractionMillis = currentMillis; 
      menuState++;
      if (menuState > 4) {
        inMenu = false; 
        break;
      }
      delay(50); 
    }
    lastSet = currentSet;

    // ---------------------------------------------------------
    // 3. UP BUTTON (Single Click + Accelerating Hold-to-Scroll)
    // ---------------------------------------------------------
    bool triggerUp = false; 

    if (currentUp == LOW) {
      if (lastUp == HIGH) { 
        // Initial Press
        triggerUp = true;
        upPressTime = currentMillis;
        upRepeatTime = currentMillis;
        currentUpRate = START_REPEAT_RATE; // Reset speed on fresh press
        delay(50); 
      } else if (currentMillis - upPressTime >= HOLD_DELAY) { 
        // Holding
        if (currentMillis - upRepeatTime >= currentUpRate) { 
          triggerUp = true;
          upRepeatTime = currentMillis;
          
          // Accelerate! (Decrease the delay between ticks)
          if (currentUpRate > MIN_REPEAT_RATE) {
            currentUpRate -= RATE_ACCELERATION;
            if (currentUpRate < MIN_REPEAT_RATE) currentUpRate = MIN_REPEAT_RATE;
          }
        }
      }
    }
    lastUp = currentUp;

    if (triggerUp && inMenu) {
      lastInteractionMillis = currentMillis; 
      
      switch (menuState) {
        case 0: isCelsius = true; break; 
        case 1: highTemp = min(highTemp + 1, 999); break;
        case 2: lowTemp = min(lowTemp + 1, 999); break;
        case 3: brightness = min(brightness + 1, 7); break;
        case 4: 
          betaValue++; 
          if (betaValue > 5000) betaValue = 1500; 
          break; 
      }
    }

    // ---------------------------------------------------------
    // 4. DOWN BUTTON (Single Click + Accelerating Hold-to-Scroll)
    // ---------------------------------------------------------
    bool triggerDown = false; 

    if (currentDown == LOW) {
      if (lastDown == HIGH) { 
        // Initial Press
        triggerDown = true;
        downPressTime = currentMillis;
        downRepeatTime = currentMillis;
        currentDownRate = START_REPEAT_RATE; // Reset speed on fresh press
        delay(50); 
      } else if (currentMillis - downPressTime >= HOLD_DELAY) {
        // Holding
        if (currentMillis - downRepeatTime >= currentDownRate) {
          triggerDown = true;
          downRepeatTime = currentMillis;
          
          // Accelerate! (Decrease the delay between ticks)
          if (currentDownRate > MIN_REPEAT_RATE) {
            currentDownRate -= RATE_ACCELERATION;
            if (currentDownRate < MIN_REPEAT_RATE) currentDownRate = MIN_REPEAT_RATE;
          }
        }
      }
    }
    lastDown = currentDown;

    if (triggerDown && inMenu) {
      lastInteractionMillis = currentMillis; 
      
      switch (menuState) {
        case 0: isCelsius = false; break; 
        case 1: highTemp = max(highTemp - 1, -99); break;
        case 2: lowTemp = max(lowTemp - 1, -99); break;
        case 3: brightness = max(brightness - 1, 0); break;
        case 4: 
          betaValue--; 
          if (betaValue < 1500) betaValue = 5000; 
          break;
      }
    }

    // ---------------------------------------------------------
    // 5. Handle Blinking Logic & Update Display
    // ---------------------------------------------------------
    if (currentMillis - previousBlinkMillis >= 500) {
      previousBlinkMillis = currentMillis;
      blinkState = !blinkState; 
    }

    char dispBuf[5]; 
    activeBrt = (brightness == 0) ? 1 : brightness;

    if (menuState < 4) {
      if (blinkState) {
        display.setIntensity(activeBrt);
      } else {
        display.setIntensity(0);
      }
    } else {
      display.setIntensity(activeBrt);
    }

    switch (menuState) {
      case 0: snprintf(dispBuf, sizeof(dispBuf), "%s", isCelsius ? "U-CE" : "U-FH"); break;
      case 1: snprintf(dispBuf, sizeof(dispBuf), "H%03d", highTemp); break;
      case 2: snprintf(dispBuf, sizeof(dispBuf), "L%03d", lowTemp); break;
      case 3: 
        if (brightness == 0) snprintf(dispBuf, sizeof(dispBuf), "bOFF");
        else snprintf(dispBuf, sizeof(dispBuf), "b- %d", brightness); 
        break;
      case 4: 
        if (blinkState) snprintf(dispBuf, sizeof(dispBuf), "%04d", betaValue);
        else snprintf(dispBuf, sizeof(dispBuf), "bEtA");
        break;
    }

    display.println(dispBuf);

    // ---------------------------------------------------------
    // 6. LED UX Logic
    // ---------------------------------------------------------
    bool canGoUp = true;
    bool canGoDown = true;

    if (menuState == 1 && highTemp >= 999) canGoUp = false;
    if (menuState == 1 && highTemp <= -99) canGoDown = false;
    if (menuState == 2 && lowTemp >= 999) canGoUp = false;
    if (menuState == 2 && lowTemp <= -99) canGoDown = false;
    if (menuState == 3 && brightness >= 7) canGoUp = false;
    if (menuState == 3 && brightness <= 0) canGoDown = false;

    digitalWrite(UP_LED, (canGoUp && currentUp == HIGH) ? HIGH : LOW);
    digitalWrite(DOWN_LED, (canGoDown && currentDown == HIGH) ? HIGH : LOW);
    digitalWrite(SET_LED, (currentSet == HIGH) ? HIGH : LOW); 
  }

  // ---------------------------------------------------------
  // 7. Cleanup & Save Indication on Exit
  // ---------------------------------------------------------
  activeBrt = (brightness == 0) ? 1 : brightness;
  display.setIntensity(activeBrt);
  display.println("SAvE");
  delay(1000); 
  //Save the values to EEPROM
  EEPROM.put(4, highTemp);     // Bytes 4, 5
  EEPROM.put(6, lowTemp);      // Bytes 6, 7
  EEPROM.put(8, isCelsius);    // Byte 8
  EEPROM.put(9, brightness);   // Bytes 9, 10
  EEPROM.put(11, betaValue);   // Bytes 11, 12
  //Disable all LEDs
  digitalWrite(UP_LED, LOW);
  digitalWrite(DOWN_LED, LOW);
  digitalWrite(SET_LED, LOW);
  
  display.setIntensity(brightness);
}

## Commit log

2024-05-22 Initial Electronics Upload
    [BOM_V2.0.1 Signal Relay Switch_V2.0.1 Signal Relay PCB_2024-05-22.xlsx, BOM_V2.0.1 USB Switch_V2.0.1 USB PCB_2024-05-22.xlsx, BOM_V2.0.1B Power Relay Switch_V2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]
2024-05-24 Updated EPRJ Files
    [BOM_V2.0.1 USB Hub Switch_V2.0.1 USB PCB_2024-05-22.xlsx, BOM_V2.0.1 USB Switch_V2.0.1 USB PCB_2024-05-22.xlsx, PickAndPlace_V2.0.1 USB HUB PCB_2024-05-22.xlsx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]
2024-05-28 Added KMX Switch
    [BOM_V2.0.1 KMX Switch_V2.0.1 PCB_2024-05-28.xlsx, PickAndPlace_V2.0.1 PCB_2024-05-28.xlsx]
2024-05-28 Updated KMX Switch
    [BOM_V2.0.1 KMX Switch_V2.0.1 PCB_2024-05-28.xlsx, PickAndPlace_V2.0.1 PCB_2024-05-28.xlsx]
2024-05-29 Added USB Adapter
    [BOM_V2.0.1_V2.0.1 PCB_2024-05-29.xlsx, BOM_V2.0.1_V2.0.1 Schematic_2024-05-29.xlsx, PickAndPlace_V2.0.1 PCB_2024-05-29.xlsx]
2024-05-29 USB Adapter Minor Fix
    [BOM_V2.0.1_V2.0.1 PCB_2024-05-29.xlsx, PickAndPlace_V2.0.1 PCB_2024-05-29.xlsx]
2024-05-29 EEPROM Programmer Initial Release
    [BOM_V2.0.1 EEPROM Programmer_V2.0.1 PCB_2024-05-29.xlsx, PickAndPlace_V2.0.1 PCB_2024-05-29.xlsx]
2024-06-04 Added Contactor Switch
    [BOM_V2.0.1 Contactor Switch_V2.0.1 PCB_2024-06-04.xlsx, PickAndPlace_V2.0.1 PCB_2024-06-04.xlsx]
2024-06-04 Update Contactor Switch
    [BOM_V2.0.1 Contactor Switch_V2.0.1 PCB_2024-06-04.xlsx, PickAndPlace_V2.0.1 PCB_2024-06-04.xlsx]
2024-06-05 Added Core Interface Board
    [BOM_V2.0.1 Interface_V2.0.1 PCB_2024-06-05.xlsx, BOM_V2.1.1 Core_V2.1.0 Core PCB_2024-05-22.xlsx, PickAndPlace_V2.0.1 PCB_2024-06-05.xlsx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]
2024-06-06 Updated AC Power Relay
    [BOM_V2.0.1B Power Relay Switch_V2.0.1B Power Relay PCB_2024-05-22.xlsx, BOM_V2.0.2 AC Power Switch_V2.0.2 PCB_2024-06-06.xlsx, PickAndPlace_V2.0.1B Power Relay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]
2024-06-07 Update Core Main Board
    [BOM_V2.1.1 Core_V2.1.0 Core PCB_2024-05-22.xlsx, BOM_V2.2.1 Core_V2.2.1 PCB_2024-06-07.xlsx, PickAndPlace_V2.1.1 Core PCB_2024-05-22.xlsx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]
2024-06-07 Cleanup for Release
    [3D_V2.0.1 PCB_2024-06-07.step, BOM_V2.0.1 Bypass Plug_V2.0.1 PCB_2024-06-07.xlsx, BOM_V2.0.1 Contactor Switch_V2.0.1 PCB_2024-06-04.xlsx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]
2024-06-10 Silkscreen Corrections
2024-10-21 Updated files for release
    [10 Deg Mount.stl, 3D_V2.0.1 PCB_2024-06-07.step, AC Case Left.stl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]
2025-01-21 Updated hardware mounts
    [10 Deg Mount.stl, Horizontal Mount.stl]
2025-02-13 Added AC Relay Safety Lock
    [powerbox_mount_drillpress.stl, powerbox_mount_flat.stl, powerbox_plugkey.stl]
2025-02-13 Added source files for plug lock
    [powerbox_mount_drillpress v1.f3d, powerbox_mount_flat v1.f3d, powerbox_plugkey v1.f3d]
2025-06-26 V2.3.2 Final Release
    [10 Deg Mount.3mf, 10 Deg Mount.stl, BOM_V2.3.2 Core_V2.3.2 LE_PCB_2024-10-21.xlsx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]
2025-06-26 Logic Connector
    [Logic Connector BOM.xlsx, Logic Connector Pick and Place.xlsx]
2025-06-26 USB Hub Switch
    [BOM_V2.0.2 USB Hub Switch_V2.0.2 PCB_2024-10-21.xlsx, USB Hub Pick and Place.xlsx, USB Hub Switch BOM.xlsx]
2025-06-26 AC Power Switch
    [AC Case Left.stl, AC Case Right.stl, AC Power Switch BOM.xlsx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]
2025-06-26 Signal Relay Swtich
    [BOM_V2.0.2 Signal Relay Switch_V2.0.2 PCB_2024-06-07.xlsx, Signal Relay BOM.xlsx, Signal Relay Pick and Place.xlsx]
2025-06-26 Expansion Card
    [Expansion Card BOM.xlsx, Expansion Card Pick and Place.xlsx]
2025-06-26 KMX Switch
    [BOM_V2.0.1 KMX Switch_V2.0.1 PCB_2024-06-07.xlsx, KMX Switch BOM.xlsx, KMX Switch Pick and Place.xlsx]
2025-06-26 Contactor Switch
    [BOM_V2.0.2 Contactor Switch_V2.0.2 PCB_2024-10-21.xlsx, Contactor Switch BOM.xlsx, Contactor Switch Pick and Place.xlsx]
2026-01-15 Moved 2.3.2 Core to new folder
    [10 Deg Mount.3mf, Core Base.3mf, Core Front Face.3mf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]
2026-01-20 SSR switch, relocated old switches
    [AC Case Left.stl, AC Case Right.stl, AC Power Switch BOM.xlsx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]
2026-01-21 Moved old "Other" devices
    [Expansion Card BOM.xlsx, Expansion Card Pick and Place.xlsx, Logic Connector BOM.xlsx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]
2026-01-22 Change to ESP32-S3
2026-01-23 USB Hub Switch Schematic Done
2026-01-27 Outjob USB Hub Switch
    [BOM_USBHubSmartSwitchV300.xlsx, PickAndPlace_USBHubSmartSwitchV300.xlsx]
2026-01-27 Reorganize SSR Switch
2026-01-27 SSR Switch Outjob
    [BOM_SSRSwitchV300.xlsx, PickAndPlace_SSRSwitchV300.xlsx]
2026-01-29 USB Hub Switch Updates
    [BOM_USBHubSmartSwitchV300.xlsx, PickAndPlace_USBHubSmartSwitchV300.xlsx]
2026-01-29 Core Interrupt Upgrade
    [BOM_NFCCoreV300.xlsx, PickAndPlace_NFCCoreV300.xlsx]
2026-01-29 4 Way Passive Splitter
    [BOM_4PortSplitter.xlsx]
2026-01-31 New AC Power Switch Schematic
2026-02-01 Started on 4 port switch
2026-02-01 Update AC Power Switch.eprj
2026-03-02 Re-organize all switch files
    [BOM_4PortSplitter.xlsx]
2026-03-06 Improved Fuse Watchdog
2026-03-11 Minor Changes, Temperature Sensor
2026-03-12 Outjob for new components
    [ACBOMV300.xlsx, MainBoardBomV300.xlsx, TemperatureSensorBOMV300.xlsx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]
2026-05-11 Update 1 Port AC Power Switch.eprj
2026-06-08 Update AC Power Switch to eprj2
2026-06-08 Update 1 Port AC Power Switch.eprj2
